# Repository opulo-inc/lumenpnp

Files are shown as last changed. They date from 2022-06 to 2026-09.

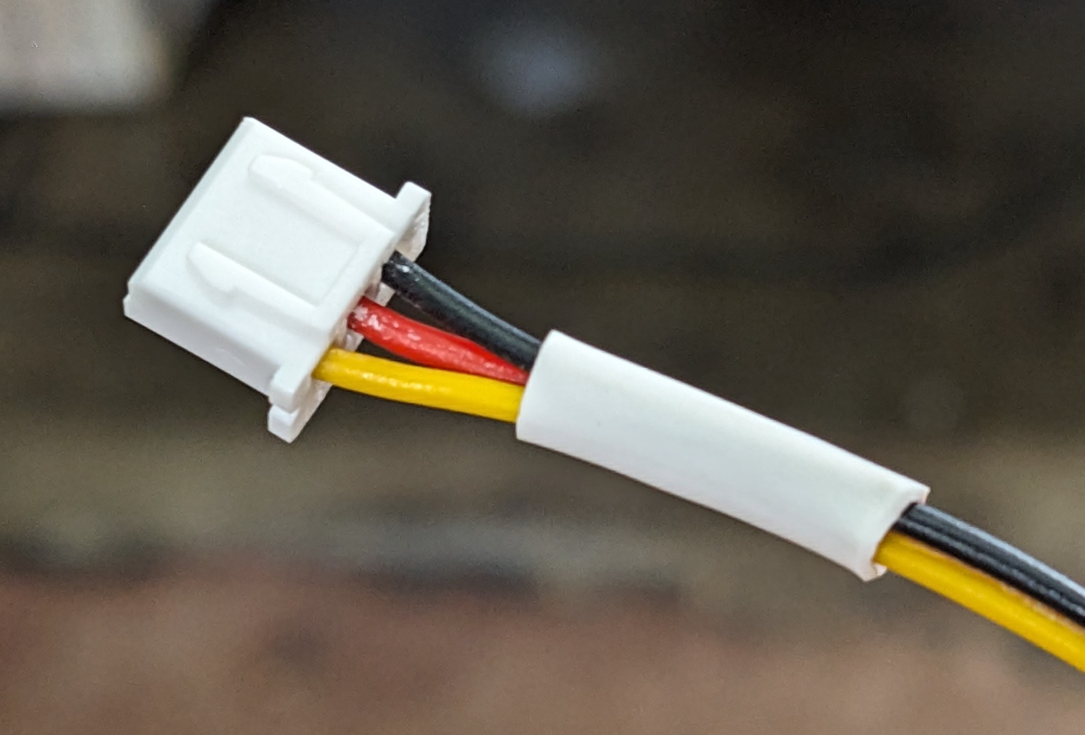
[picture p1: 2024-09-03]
src/CHA/img/label.png

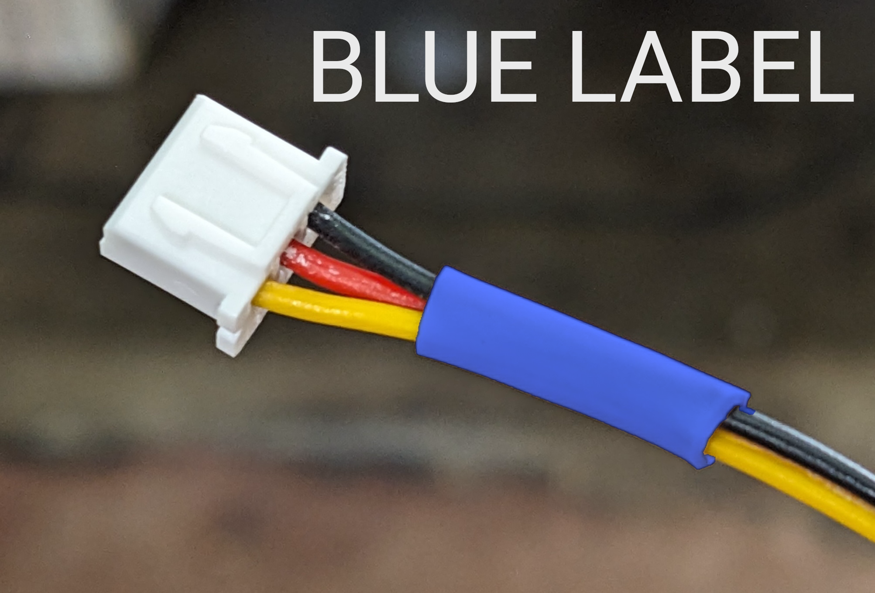
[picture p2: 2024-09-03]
src/CHA/img/label-blue.png

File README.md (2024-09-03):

# LumenPnP

The LumenPnP is an open source [pick and place machine](https://en.wikipedia.org/wiki/Pick-and-place_machine) that reliably and accurately assembles electronic components onto circuit boards.

v4

The LumenPnP is available for sale on the [Opulo Website](https://www.opulo.io/products/lumenpnp). Machines are being used in active production daily. If you build or buy one, please help the project by documenting bugs with a GitHub issue.

**Please [read the wiki here](https://github.com/opulo-inc/lumenpnp/wiki)!** The wiki covers information about the state of the project, contributing instructions, and frequently asked questions.

Along with the pick and place machine itself, the project also includes feeders designed to work with the machine. The source for powered feeders can be found [in their separate repository](https://github.com/opulo-inc/feeder).

For exported versions of the source (STLs, schematic PDFs, compiled binaries, etc), you can find them attached to the [latest release](https://github.com/opulo-inc/lumenpnp/releases).

The LumenPnP's development process is being cataloged in a series of videos. A playlist of these can be found [here](https://www.youtube.com/playlist?list=PLIeJXmcg1baLBz3x0nCDqkYpKs2IWGHk4).

## How do I get one?

You can buy a machine on the [Opulo Website](https://www.opulo.io/products/lumenpnp)!

## Contributing

If you would like to contribute to the project, awesome! Check out the [contributing page](https://github.com/opulo-inc/lumenpnp/wiki/Contributing) to get started.

## Community

Discussion about the project happens on the [LumenPnP Discord server](https://discordapp.com/invite/TCwy6De)!

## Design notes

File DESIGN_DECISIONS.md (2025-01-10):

# LumenPnP Design Decisions

This page aims to illustrate the design decisions behind the LumenPnP. The design process started in early 2020, and has seen hundreds of iterations and approaches. This page gives background about why things are done the way they are, to help communicate to folks new to the project what has been tried, and why it was not chosen.

## Overview

The LumenPnP is a mostly 3D printed desktop pick and place machine. It has two nozzles on the head. There are two built-in cameras and ring lights for top and bottom vision. These are used for fiducial calibration of the board being populated and part rotation/offset calibration on the nozzle. It is capable of populating boards as large as 225mm x 400mm.

The LumenPnP is comprised of v-slot aluminum extrusion for most of the structural members in the machine, connected together using aluminum brackets and 3D printed parts. The X gantry rides on two Y gantries, and v-slot wheels are used for linear motion in the machine. The main build area of the machine is comprised of staging plates, which are 120mm x 600mm PCBs with a [Peek Array](https://www.crowdsupply.com/sutajio-kosagi/novena) for mounting machine parts and strip feeders.

## Axis of Motion

There are five axes of motion in a stock LumenPnP:

- The X linear axis is driven by a NEMA 17 stepper motor that pulls the X gantry along an MGN12H linear rail using a GT2 timing belt.
- The Y linear axis is similar, but uses two two NEMA 17 stepper motors and two MGN12H linear rails. These motors are independently driven by two stepper drivers as of v4.0.0.
- The Z linear axis is mounted to the X gantry and also uses a NEMA 17 stepper motor, but pulls two counterweighted Z gantries along short LML9B linear rails.
- The A & B rotational axes are mounted to the Z gantries and each use a NEMA 11 stepper motor with a hollow shaft. These pass the vacuum through to the nozzles used to pick and place parts.

### V-rollers vs linear rails

V-slot rollers are small wheels designed to ride inside the V-slots on aluminum extrusions. They're an inexpensive means to support and constrain the motion of a linear axis. They became very popular due to being used on mass market 3D printers such as the Ender 3. Linear guide rails, on the other hand, are solid steel rails coupled with a carriage block containing ball bearings. Linear rails require less maintenance and perform significantly better than V-rollers, but have typically been too expensive for hobbyist machines.

Due to this, V3.0.5 and earlier versions of the LumenPnP used V-rollers for the X and Y linear axes. However, times changed and 3D printers began competing on speed which necessitated linear rails - making them much easier and cheaper to source. As a result, Opulo switched the LumenPnP to linear rails going forward.

If you want to replace the V-rollers on an existing LumenPnP with linear rails you can use [Stargirl's mod](https://www.printables.com/model/278803-lumenpnp-linear-rail-mods-v3).

### Why not CoreXY?

CoreXY offers the possibility of faster movement by removing a heavy motor from one of the gantries, keeping the head very light and easy to accelerate.

However, switching to a CoreXY configuration would actually *remove* a motor from the current system. The current solution has two separate stepper motors dedicated to moving the Y gantry, and one motor for the X gantry. CoreXY would reduce this to only two motors shared across both axis, which actually results in an lower average acceleration.

Also, CoreXY has a much more complicated belt routing path than with a separate X and Y axis configuration. Keeping axes separate allows Opulo to ship each axis packaged separately, meaning belts are pre-routed making assembly much easier.

### Why not a NEMA 8 hollow shaft for part rotation?

In the early days of design, we struggled to find a full 360 degree pneumatic coupler for 4mm PU tubing with a M5 threading at a decent price that didn't leak like a sieve. This coupler was meant to thread into the top of the hollow-shaft steppers that rotate parts on the nozzles. Because we couldn't get a good coupler, we were forced to limit the A and B axis rotation to plus or minus 180 degrees as to not tangle up the tubing, as opposed to being able to rotate any amount in any direction. Even then, the tubing provided enough resistance to rotation that a beefier stepper was required to ensure we weren't skipping steps when rotating nozzles.

Since then, the community has found sources for much better couplers that eliminate this problem. With almost no resistance to rotating nozzles, much smaller motors can be used. This is an update Opulo is actively exploring rolling into production, especially in conjunction with a linear rail/CoreXY update where the benefit of this weight reduction would be realized.

## Firmware

The LumenPnP runs stock Marlin firmware. Marlin was originally designed to control 3D printers, but it works spectacularly for controlling a pick and place machine. We've added a couple features to Marlin to support pick and place specific functions, namely reading vacuum sensors and communicating to feeders.

### Why not a different firmware project?

There exist many different 3D printer/CNC firmware projects, of which a number would likely work well for a pick and place. We ended up choosing Marlin for a number of reasons.

The first and primary reason for choosing Marlin is the ease of adding new hardware to mainline. Marlin supports hundreds of different controller boards, and adding a new one is a well understood process. This also means any pick and place specific features we add upstream are able to be used by folks on hundreds of other hardware designs.

Other options like Klipper would definitely fulfill the requirements of the project, but many of the features of these other options are unnecessary for a pick and place application.

## Motherboard

The LumenPnP motherboard is a custom controller based on the STM32F407VET6 microcontroller. It has support for up to 6 axis of motion, four pumps or valves, two vacuum sensors, two WS2812 busses, an RS-485 port for feeder communication, and an AUX port for peripherals.

### Why not off the shelf?

Some off the shelf boards would work great for the core functionality of a pick and place. We wanted to provide new features specific to pick and place machines that are not available in other hardware. The main features we wanted to add were vacuum sensors for detecting if parts have been successfully picked, and a port to provide power and communication for feeders.

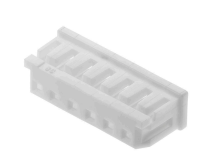
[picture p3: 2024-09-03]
src/CHA/img/molex-51065-0600.png

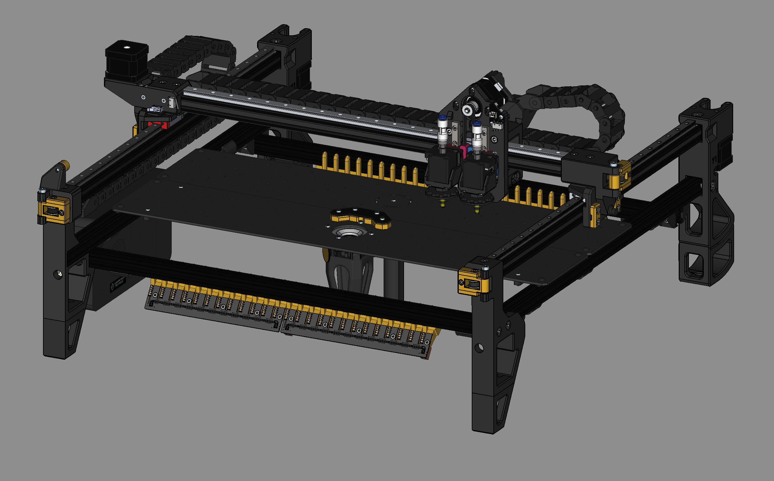
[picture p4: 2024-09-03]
img/v4-cad-hero.png

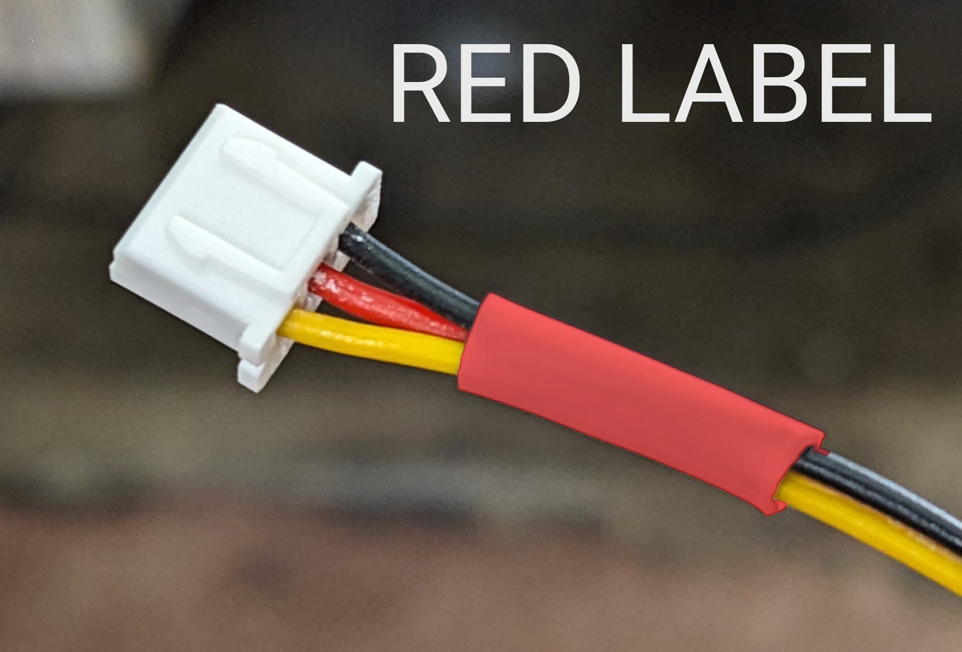
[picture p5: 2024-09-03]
src/CHA/img/label-red.png

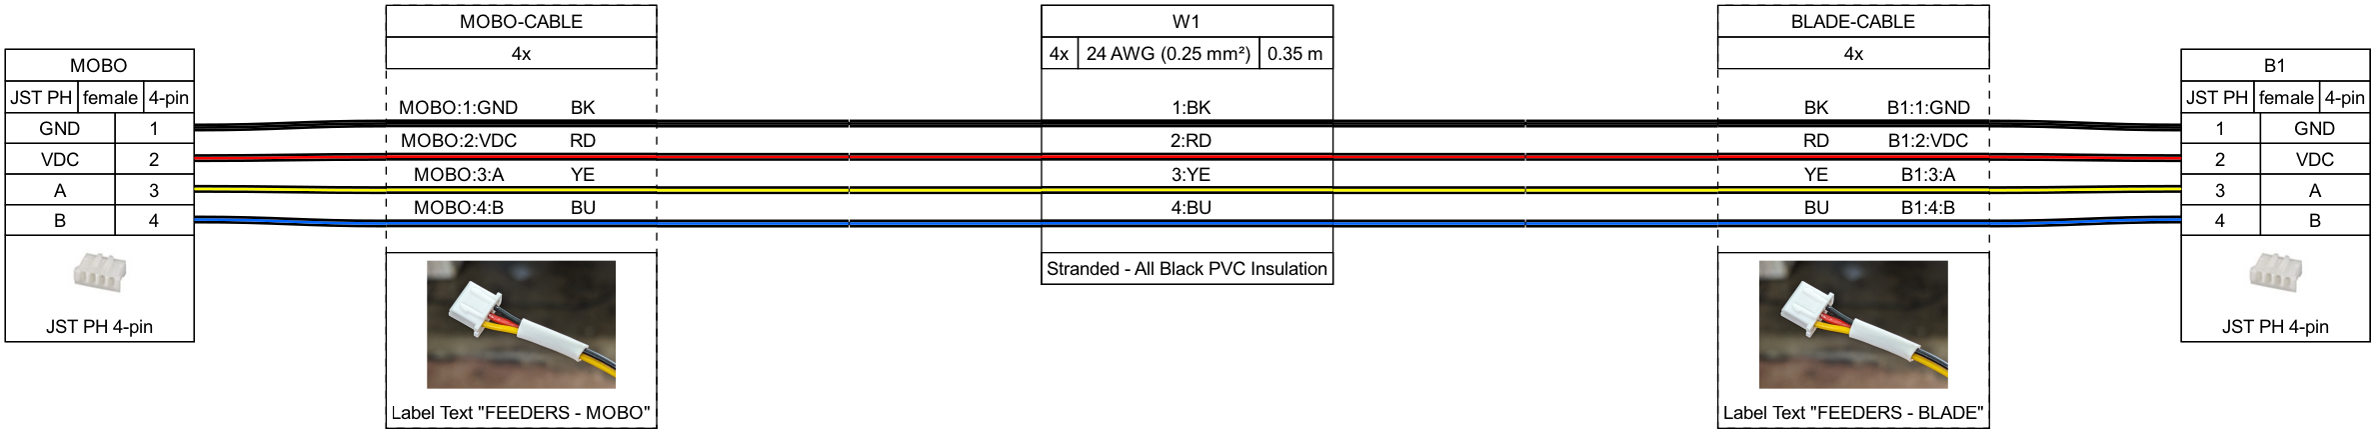
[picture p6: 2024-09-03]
src/CHA/mobo-blade1/mobo-blade1.png

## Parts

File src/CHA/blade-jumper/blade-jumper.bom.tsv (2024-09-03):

Id | Description | Qty | Unit | Designators
1 | Cable, 4 x 24 AWG | 0.04 | m | W1
2 | Connector, JST PH, female, 4 pins | 2 |  | J1, J2

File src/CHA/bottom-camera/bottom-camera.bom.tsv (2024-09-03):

Id | Description | Qty | Unit | Designators
1 | Cable, 4 x 24 AWG | 0.7 | m | W1
2 | Connector, JST ZH, female, 4 pins | 1 |  | BC-C
3 | Connector, USB TYPE A, male, 4 pins | 1 |  | BC-H
4 | Wire, BK | 0 | m | BL-H-CABLE, BL-M-CABLE
5 | Wire, RD | 0 | m | BL-H-CABLE, BL-M-CABLE
6 | Wire, YE | 0 | m | BL-H-CABLE, BL-M-CABLE

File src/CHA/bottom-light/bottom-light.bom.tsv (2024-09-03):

Id | Description | Qty | Unit | Designators
1 | Cable, 3 x 24 AWG | 0.35 | m | W1
2 | Connector, JST PH, female, 3 pins | 1 |  | BL-M
3 | Connector, JST XH, female, 3 pins | 1 |  | BL-H
4 | Wire, 22 AWG, RD | 3.1 | m | BL-H-CABLE, BL-M-CABLE
5 | Wire, 22 AWG, WH | 3.1 | m | BL-H-CABLE, BL-M-CABLE
6 | Wire, 22 AWG, YE | 3.1 | m | BL-H-CABLE, BL-M-CABLE

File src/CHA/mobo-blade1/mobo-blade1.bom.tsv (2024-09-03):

Id | Description | Qty | Unit | Designators
1 | Cable, 4 x 22 AWG | 0.8 | m | W1
2 | Connector, JST PH, female, 4 pins | 2 |  | B1, MOBO

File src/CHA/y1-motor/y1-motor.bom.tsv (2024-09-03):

Id | Description | Qty | Unit | Designators
1 | Cable, 4 x 22 AWG | 0.8 | m | W1
2 | Connector, JST PH, female, 6 pins | 1 |  | X2
3 | Connector, JST XH, female, 4 pins | 1 |  | X1

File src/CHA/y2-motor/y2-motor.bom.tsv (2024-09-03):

Id | Description | Qty | Unit | Designators
1 | Cable, 4 x 22 AWG | 1.2 | m | W1
2 | Connector, JST PH, female, 6 pins | 1 |  | X2
3 | Connector, JST XH, female, 4 pins | 1 |  | X1

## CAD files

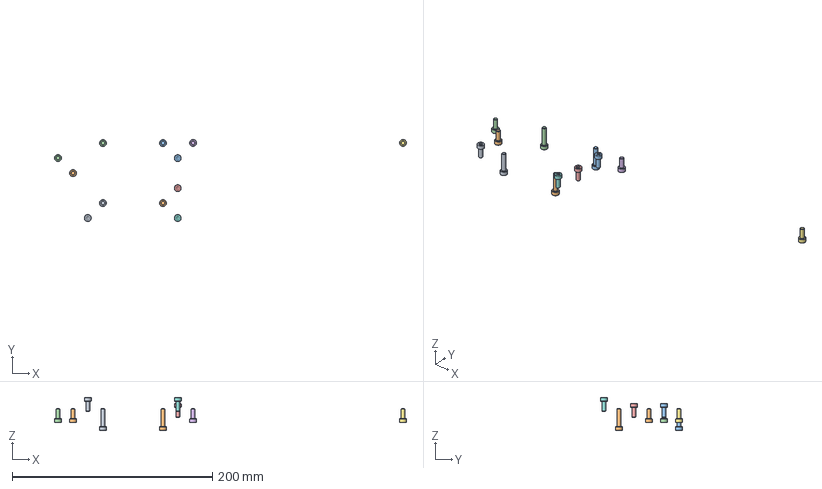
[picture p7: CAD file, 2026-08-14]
src/ASM/staging-plate-ASM.FCStd
352.0 x 82.1 x 33.3 mm
M4x18-Screw
M4x10-Screw
M4x10-Screw002
M4x10-Screw004
M4x10-Screw006
M4x10-Screw008
M4x10-Screw010
M4x10-Screw012
M4x10-Screw014
M4x18-Screw002
M4x18-Screw004
M4x18-Screw006

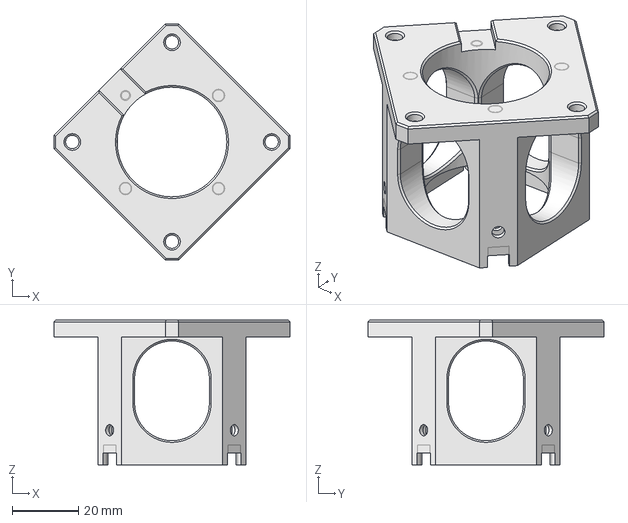
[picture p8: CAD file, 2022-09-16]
pnp/cad/FDM/bottom-camera-mount.FCStd
71.0 x 71.0 x 43.5 mm

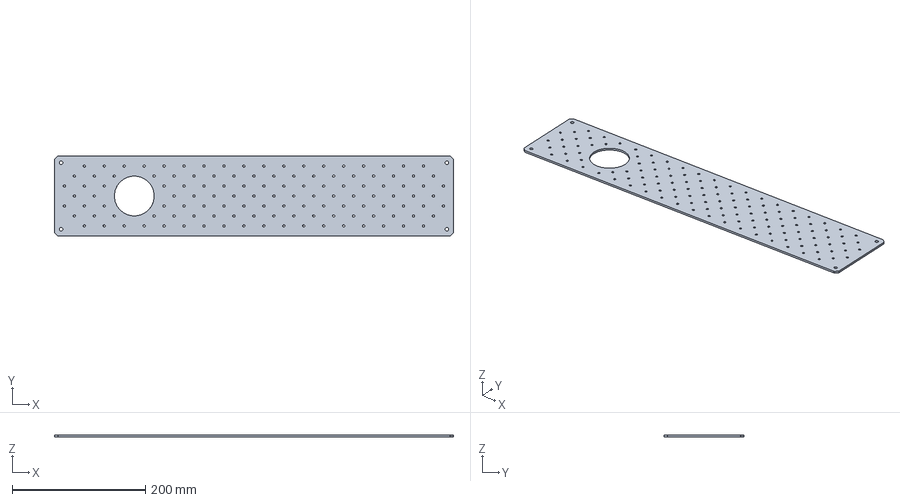
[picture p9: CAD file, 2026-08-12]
src/CSM/staging-plate-offcenter.FCStd
600.0 x 120.0 x 3.00 mm

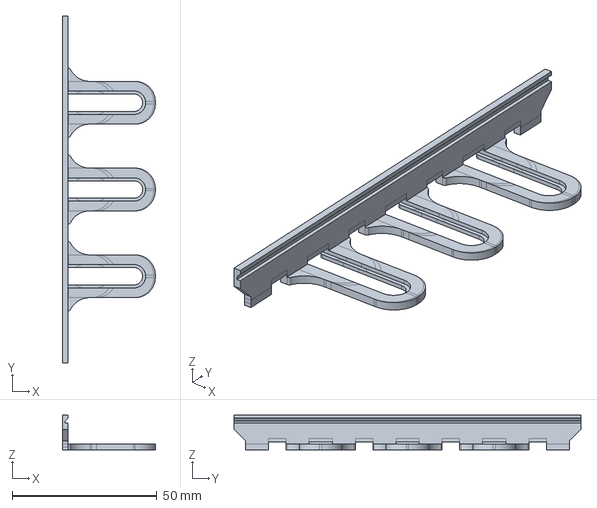
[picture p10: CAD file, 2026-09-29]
src/FDM/adj-strip-feeder-left.FCStd
32.1 x 120.0 x 12.0 mm

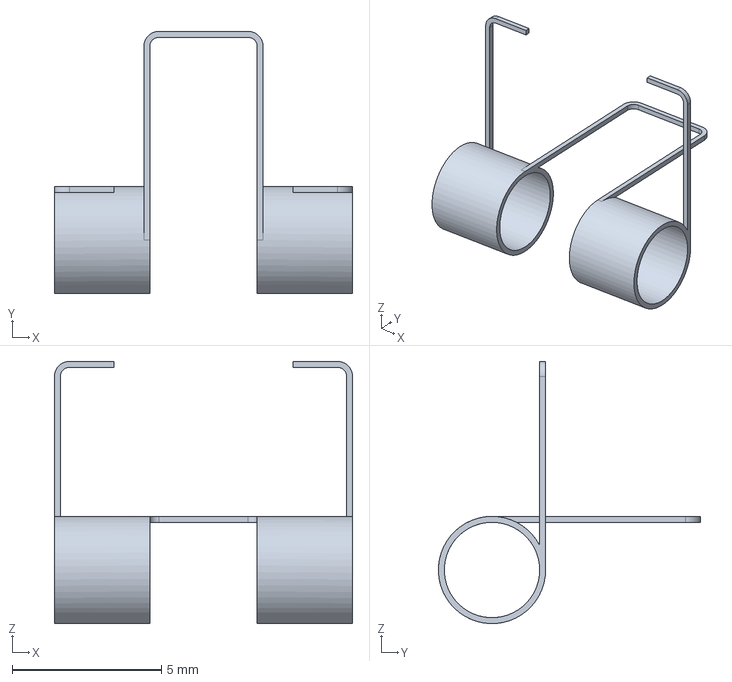
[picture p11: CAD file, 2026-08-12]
src/OTS/dt-spring-pick-window.FCStd
10.0 x 8.80 x 8.80 mm

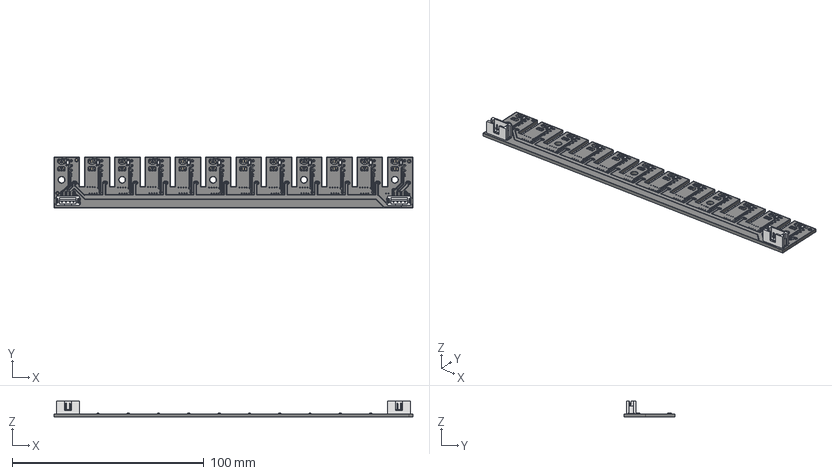
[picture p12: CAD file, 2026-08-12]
src/PCB/blade12/blade12-PCB.FCStd
187.2 x 26.6 x 8.22 mm
Pcb_f782
topPads_f782
topTracks_f782
topZones_f782
botPads_f782
botTracks_f782
botZones_f782
${REFERENCE}_R_0805_2012Metric_null x 12
${REFERENCE}_B4B-PH-SM4-TB_null[2] x 2

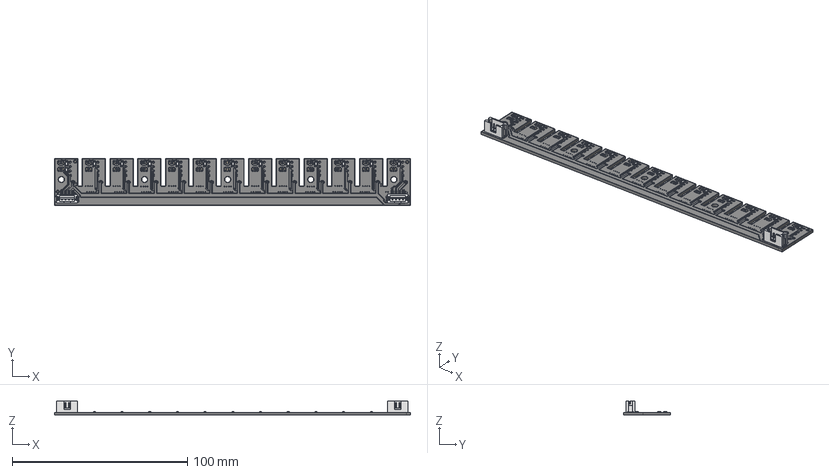
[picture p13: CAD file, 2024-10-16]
src/PCB/blade13/blade13-PCB.FCStd
203.0 x 26.6 x 8.22 mm
Pcb_e7a3
topPads_e7a3
topTracks_e7a3
topZones_e7a3
botPads_e7a3
botTracks_e7a3
botZones_e7a3
${REFERENCE}_R_0805_2012Metric_null x 14
${REFERENCE}_B4B-PH-SM4-TB_null[2] x 2

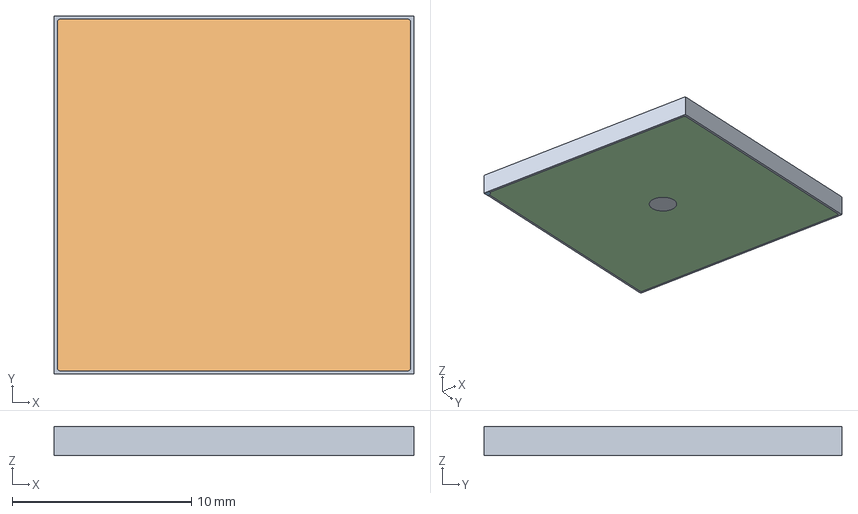
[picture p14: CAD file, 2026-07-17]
src/PCB/cal-fid/cal-fid.FCStd
20.0 x 20.0 x 1.63 mm
Pcb_c21e
topZones_c21e
botPads_c21e_cut
botZones_c21e

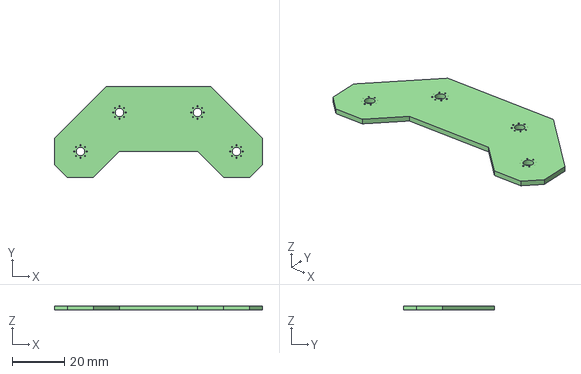
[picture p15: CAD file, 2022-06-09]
src/PCB/datum/datum-board.step
80.0 x 35.0 x 1.60 mm

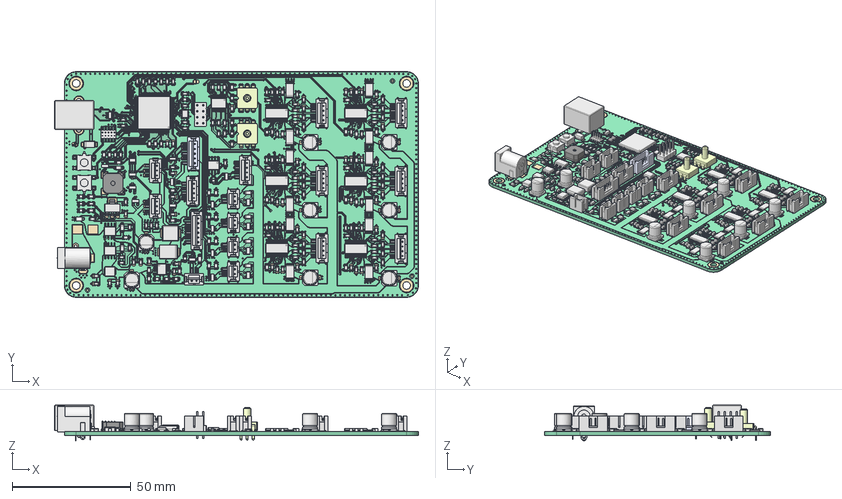
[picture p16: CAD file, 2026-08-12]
src/PCB/mobo/mobo-REV05.FCStd
153.1 x 95.0 x 15.0 mm
Pcb_270f
topPads_270f
topTracks_270f
topZones_270f
botPads_270f
botTracks_270f
botZones_270f
C19_C_0805_2012Metric_dd7fe1078c82 x 116
U2_SO-8_3.9x4.9mm_P1.27mm_18ac448d4230 x 2
C18_CP_Elec_63x77_ff28b986d17e x 8
J18_B2B-PH-SM4-TB_b9beb4a1e8ac[2] x 5
J5_B4B-PH-SM4-TB_7cb4547b0ad5[2] x 8
R61_R_0805_2012Metric_702471a57eb5 x 58
L2_L_Sunlord_MWSA0402S_521b67255e56
Q6_SOT_23_7e3c471798a1 x 13
D7_D_SOD_123F_3f376ee7206a x 6
R32_R_2512_6332Metric_fd8a2fdd02c5 x 12
U21_TSOT_23_401a1807623d x 4
J17_B5B-PH-SM4-TB_ce0894eb786b[2]
BZ1_CUI_DEVICES_CMT-8504-100-SMT-TR_9afe1c6a999b[2]
L12_L_0805_2012Metric_ae928abe879c x 24
J13_B6B-PH-SM4-TB_f104a4ad5df6[2]
U15_SOIC_8_39x49mm_P127mm_9e3604cb9ea4 x 2
D3_D_SOD_123_7fd80e287a01 x 2
D19_D_SMA_ff0e973445e4
U17_TSSOP_20_44x65mm_P065mm_3a2178bb8b3e
D1_D_SMC_db09bdd7a7d4
U12_SOT_23_6_22d69487b26d x 2
SW1_B3S_110[]_fa0ae1ab19d8[2] x 2
J7_BarrelJack_Horizontal_6e7f0b02579b
U10_HTSSOP_28_1EP_44x97mm_P065mm_9ebe34d6a526 x 6
D20_D_SMF_c34d6fe6dce6
U5_LQFP_100_14x14mm_P05mm_e908b35d191a
D5_LED_0805_2012Metric_18e83e1d4d5c x 3
J2_PinHeader_2x05_P127mm_Vertical_SMD_7237c33a1887
J9_B3B-PH-SM4-TB_472ac10851bf[2] x 2
L1_L_Sunlord_MWSA0603S_998824e03534
J14_PinHeader_2x04_P254mm_Vertical_97425652c6a4
Y1_Crystal_SMD_3225-4Pin_3.2x2.5mm_5af4ee45a679
U4_SOT_223_0cafcd1d99c6
XGZP6857D200KPGPN33_002
XGZP6857D200KPGPN33_001
USB type-B female PCB

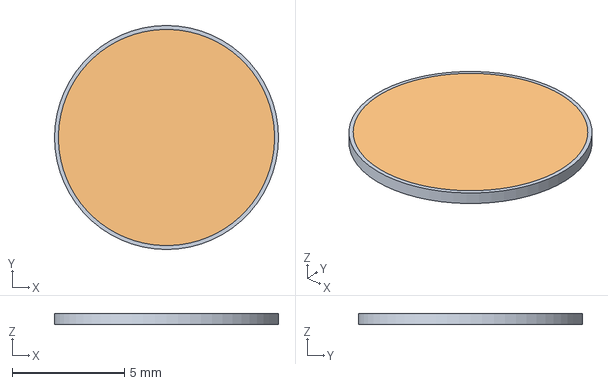
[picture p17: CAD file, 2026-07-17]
src/PCB/nozzle-cal-token/nozzle-cal-token.FCStd
10.0 x 10.0 x 0.51 mm
Pcb_83d9
topZones_83d9

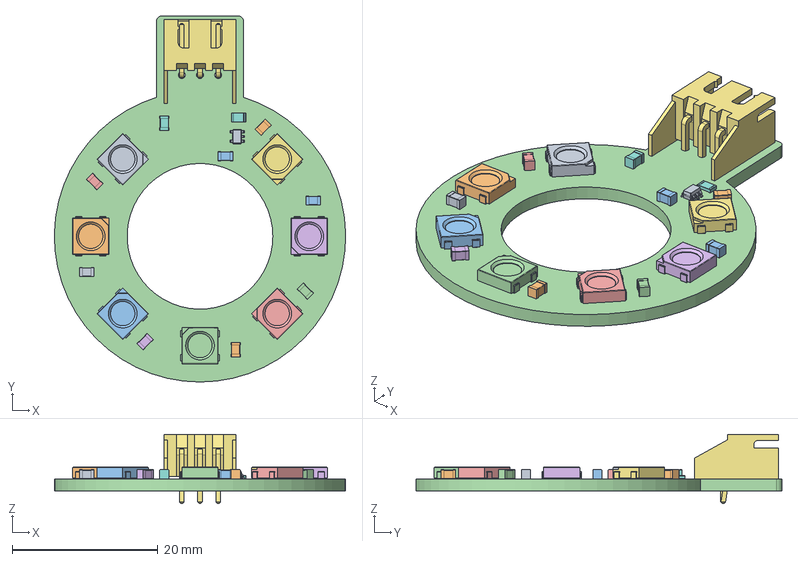
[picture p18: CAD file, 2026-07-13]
src/PCB/ringLight/bottom-ring-light.FCStd
40.0 x 50.2 x 9.50 mm
bottom-ring-ligh-pcb001

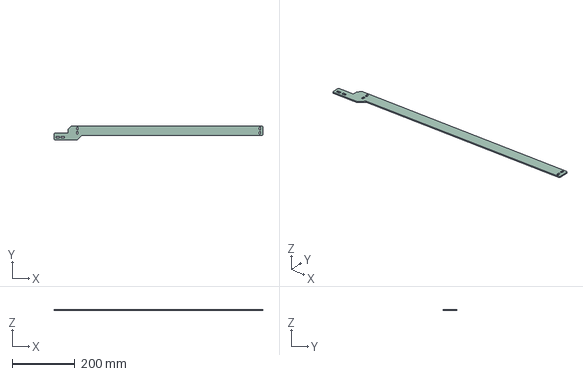
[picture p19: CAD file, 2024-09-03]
src/PCB/x-cable-chain-support/x-cable-chain-support.step
664.0 x 44.5 x 3.00 mm

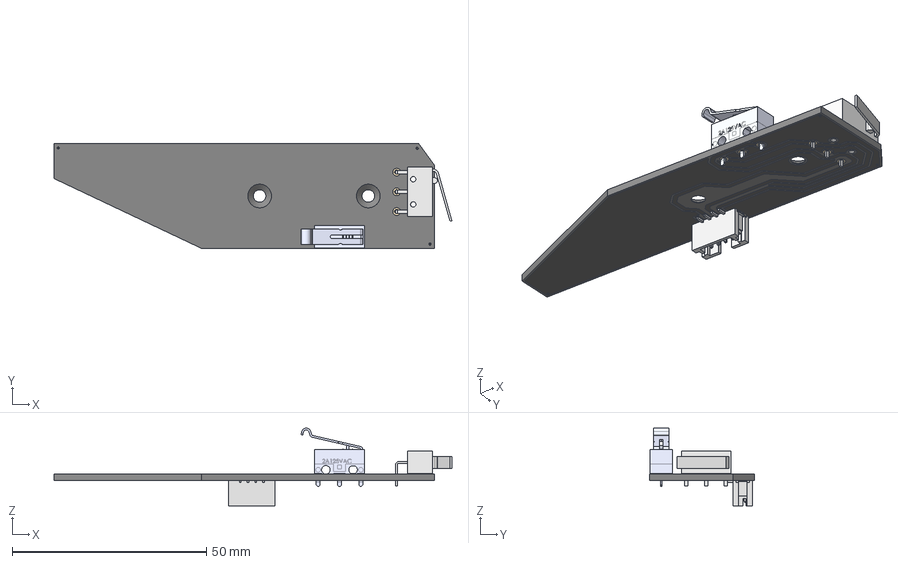
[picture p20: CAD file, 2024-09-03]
src/PCB/xy-limit/xy-limit.FCStd
102.6 x 27.0 x 20.1 mm
topPads_14f9
botPads_14f9
botTracks_14f9
botZones_14f9
Pcb_14f010
SW2_Limit_Switch_SPDT_sim_roller_8e450556c7f0
SW1_Body_0292104bbb26
J2_B4B-PH-SM4-TB_56e32e6460db[2]

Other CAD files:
src/ASM/board-mount-dynamic-ASM.FCStd
src/PCB/z-limit/z-limit.FCStd
pnp/cad/FDM/x-gantry-back.FCStd
src/CSM/build-plate.FCStd
src/FDM/12mm-strip-feeder.FCStd
src/FDM/16mm-strip-feeder.FCStd
src/FDM/24mm-strip-feeder.FCStd
src/FDM/32mm-strip-feeder.FCStd
src/FDM/8mm-strip-feeder.FCStd
src/FDM/adj-strip-feeder-right.FCStd
src/FDM/back-leg-extension.FCStd
src/FDM/back-leg.FCStd
src/FDM/belt-clamp.FCStd
src/FDM/belt-tension-arm.FCStd
src/FDM/blade12.FCStd
src/FDM/blade13.FCStd
src/FDM/board-mount-dynamic.FCStd
src/FDM/board-mount-flap.FCStd
src/FDM/board-mount-static.FCStd
src/FDM/board-support.FCStd
src/FDM/bottom-camera-mount.FCStd
src/FDM/bottom-light-mount.FCStd
src/FDM/bottom-vision-cable-clamp.FCStd
src/FDM/bottom-vision-cover.FCStd
src/FDM/cable-splay.FCStd
src/FDM/cal-fid-mount.FCStd
src/FDM/control-box-lid.FCStd
src/FDM/control-box.FCStd
src/FDM/datum-board-mount.FCStd
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

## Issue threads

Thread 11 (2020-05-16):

Change carriage bottom rollers mounting for eccentric nut

Frzoen, 2020-05-16:
Change design of the carriages to use eccentric nut.
ie. this [Eccentric Spacers - Amazon](https://www.amazon.com/PSCCO-Eccentric-Spacers-Wheel-Printer/dp/B083YTJ7S3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)

This will help in tightening the carriage rollers onto aluminium profiles.
This is also opportunity to change the design to use one less roller/carriage by changing square pattern to triangle. This shouldn't impact stability of carriage and help tightening BOM.

sphawes, 2020-05-16:
I love these things, but I'm concerned about their usage here. Instead of being inserted into a hole on a nice piece of steel, they'd be going into a hole on an FDM part. I'm not currently super happy with the current slot method, so definitely looking for an alternative, but these in a printed part might end up causing problems. Are there other types of tensioning we could use for these rollers? Or maybe some way we could have these eccentric spacers slot into something a bit more substantial?

Frzoen, 2020-05-16:
Just finished design for eccentric nut.

I will print it and test with one salvaged from my printer. Will get in touch soon with test resoults

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

Frzoen, 2020-05-16:
Maybe mounting mechanism similar to this from EleksMaker featured in Marco Reps's videos?
[mentioned video](https://youtu.be/1hFNj86L7sk?t=120) (mind the goat).

There is sheet of acrylic... maybe 3d print will be similar in strength.

Frzoen, 2020-05-17:
Ok, so after first test that looks promising.

For now i cannot test it with stepper motor but i tried to break it using a lot of force and taking advantage of the lever with 2020 profile and I could't break it.

Right now i will adjust the height of the spacers for the v-slot rollers.

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

G-Pereira, 2021-02-14:
As discussed this change would require increased maintenance since the nuts would loosen over time and also not the best to use against FDM parts.

Closed 2021-02-14.

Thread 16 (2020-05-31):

Suggestion to change nema11 hollow shaft to a different system for angular positioning

Arthur-Silveira, 2020-05-31:
I was thinking about changing the Nema11 with hollow shaft to a different angular positioning system.
It seems to be very difficult to find such a motor here in Brazil, so I'm planning on using the same standard NEMA17 used on other axes.
I will try the approach on this drawings (really sorry for the ultra low quality on hand drawing, absolutely nothing is on scale).

Any thoughts to improve this idea??

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

Arthur-Silveira, 2020-05-31:
Nevermind for this suggestion.
I'll have to import the nozzle and nozzle adapter anyways, so I will just add the motor to the list as well.

I'm thinking about this kit from Aliexpress instead of the RobotDigg suggested on the BOM

https://www.aliexpress.com/item/4000090366591.html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,scm-url:1007.13338.170725.0,pvid:1c21acfd-dd72-44ef-a7ba-3e56ca9c6147,tpp_buckets:668%230%23131923%2316_668%23808%234093%23765_668%23888%233325%2315_3338%230%23170725%230_668%232846%238111%23469_668%232717%237565%23778

bjonesrock, 2020-06-01:
I'm working on putting together a pnp as well, and didn't want to buy the RobotDigg kit either. I bought NEMA8 steppers with hollow shafts, and juki nozzles from ebay and then bought quick connect fittings with 1/4" NPT threads.

I printed a cap that screws into one side of the NEMA8 motor with M2x20 screws and then the quick connector fitting screws into the cap. Super cheap and simple way to replace the swivel adapter with a common part and a 3d printed part.

I also printed an adapter to connect the 5mm hollow NEMA8 shaft to the 7mm Juki shaft, but it's not perfectly centered, which I don't like.

Here are some photos and the STEP files for the NEMA8 cap and the Juki adapter.
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
[juki-nema8-connectors.zip](https://github.com/sphawes/index/files/4711643/juki-nema8-connectors.zip)

Arthur-Silveira, 2020-06-02:
Hi bjonesrock,

> I printed a cap that screws into one side of the NEMA8 motor with M2x20 screws and then the quick connector fitting screws into the cap. Super cheap and simple way to replace the swivel adapter with a common part and a 3d printed part.

Printing that cap seems to be a very good low cost option to replace the swivel connector. It might add some vacuum losses due to air leaking through the motor, but not sure if enough to affect operation.
I will definetely give a try to your idea before purchasing the Aliexpress one. I think I might find a similar motor here. This way i will only have to buy the nozzle from ebay or Ali.

> I also printed an adapter to connect the 5mm hollow NEMA8 shaft to the 7mm Juki shaft, but it's not perfectly centered, which I don't like.

Yeah, I'm very concerned about the angular repeatability due to the misalignment. I've seen someone complaining about this on that aliexpress solution I've posted the link previously as well (posting that it would make not viable to place even 0603 components, even using the original Juki adapter).

I was wondering if we could add extra support with a ball bearing on one of those positions (see picture below). The problem on the extra support on the red arrow is that it will make very difficult to change the nozzle, so probably on the blue arrow is better.

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

bjonesrock, 2020-06-02:
Additional support would probably help, but it's not that long. The hollow end of the stepper shaft is basically right up against the back of the juki nozzle. I wonder if I used a resin printer if the tolerances would be better. I feel like the coupler just isn't straight enough.

Arthur-Silveira, 2020-06-03:
I see your coupler is quite simple. I though it originally had more inner details to fit the nozzle.

Have you considered just printing a simple cylinder with a single and slightly smaller hole (say 4mm) in the middle, then drill the entire piece for 5mm , and then backdrill only partially for the bigger  (7mm) hole for the nozzle?
I believe it might reduce the centering misalignment (of course, depending of the bit drill and driller quality).
Or if you have access to a turning machine, even better just machine the entire part from a solid piece of nylon, of course.

Maybe another possible try is to use a commercial 5x7 shaft coupling and then cover it with some tape to keep vaccum inside.
(like https://pt.aliexpress.com/item/32826916374.html)

bjonesrock, 2020-06-03:
All good ideas. No I haven't tried just drilling it out, I'll give that a go tomorrow and see how it works. I wish I had a lathe, though I haven't had many good reasons to get one.

Hmm those flexible adapters have slots cut out which would need to be covered with some electrical tape. I just bought a pair from Amazon and will test it out

Thanks!

bjonesrock, 2020-06-03:
I tried printing it with slightly smaller holes and then drilling it with M5 and M7 drill bits on my drill press and it's not any better.

I also then tried drilling a small piece of wood with the M5 bit, and then in the same hole drilling halfway through with an M7 bit and that wasn't any better either.

The 5mm to 7mm coupler comes in the mail tomorrow and I'll let you know how that goes.

I haven't used Open PNP before, but using the bottom camera could it compensate for an off center rotation with the upward facing camera?

plasticuser, 2020-06-04:
I wonder why NEMA 11 was chosen to replace NEMA 8? Is the NEMA 8 underpowered? It has the same accuracy, is lighter and draws less power than the 11. It’s a bit quicker too.

Mostly, it’s available from many more outlets in the hollow shaft variant.

It would be helpful to know the reason behind the decision, so we can buy the right parts and move on.

bjonesrock, 2020-06-05:
Yeah NEMA 8 motors make way more sense to me and seems to be what most people use. The flexible adapters aren't coming until Saturday so I tried adding 3 screws around the 3d printed coupler to see if I could straighten it out. But it's still not great.
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

plasticuser, 2020-06-05:
The NEMA 8 are a fair bit lighter than the NEMA 11 versions, so I suspect the carriage lift/return would manage much better acceleration.

bjonesrock, 2020-06-08:
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

I finally got the 5mm to 7mm coupler in the mail.

It works great! It spins nice and centered. You just have to put some pressure down on the coupler as you tighten it so everything stays nice and square

Here is a link to the coupler I bought off Amazon https://www.amazon.com/dp/B0816JQBYZ/ref=cm_sw_r_other_apa_i_3zS3EbKDBYFMK

bjonesrock, 2020-06-08:
Uhh actually scratch that. The flexible coupler is solid in the center. I tried drilling a hole in the rubber plastic center and putting electrical tape around the coupler but when I blow through the hollow motor shaft the air escapes through the sides of the coupler

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

Arthur-Silveira, 2020-06-17:
> Uhh actually scratch that. The flexible coupler is solid in the center. I tried drilling a hole in the rubber plastic center and putting electrical tape around the coupler but when I blow through the hollow motor shaft the air escapes through the sides of the coupler
>

Maybe using this kind of commercial coupler would be beter to avoid leakage. Some tape over the grooves (even over screws) seems to be enough.
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

Unfortunately, I've not yet managed to find a suitable hollow shaft motor here in BR.
For now, I will wait for the complete kit I've purchased on Ali (https://pt.aliexpress.com/item/4000090366591.html) as amazon is not an option for me.
If anyone else find suitable options on Chinese vendors, that would be welcome.

Also, hoping the bottom camera could adequately compensate for some deviations due to misalignment.

bjonesrock, 2020-06-17:
Yeah that style adapter seems like it might work better. I tried another 3D printed adapter that has 2 flanges that an M2 screw goes into to pull the coupler tight, but it was slightly off center as well.
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
bjonesrock, 2020-06-29:
Yeah that might do the trick. In the US we call that Plumber's Putty. I've got some plasticine clay on hand, maybe that'll work. I had to rotate the part in order to print it without supports so it has lots of layer lines which makes sense why it wouldn't seal very well.

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

Arthur-Silveira, 2020-06-30:
If it is also leaking between the layers even with finer layer steps (0.1 mm layer for example) maybe some paint or coating might help reducing the leakage. Maybe some spray painting, or nail polish ? Never tried painting PLA before.. there might be some preferred options that best adhere to PLA plastic.

This seems very good, but very specific though
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
 https://3druck.com/3d-druckmaterialien/xtc-3d-verleiht-3d-gedruckten-objekten-eine-ebenmaessigere-oberflaeche-3028167/

I would give a try with nail polish + commercial Oring (to avoid the mess with the Plumber's putty) as 1st option, since they seem commercially available everywhere.

bjonesrock, 2020-06-30:
I put a thin layer of clay between the 3D print and the NEMA8 motor and that sealed it really well :)

Plumber's putty is pretty common, but clay works just as well. Smoothing the part might work, but PLA is harder to smooth.

Since I rotated the part to 3D print it the tolerance on the push to connect adapter was a little loose so I wrapped some more teflon tape. I'll tighten up the part and try printing it again and upload the file soon

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

bjonesrock, 2020-07-01:
Alright I tightened the hole that the push to connect fittings screw into so you don't have to seal it with extra teflon tape. Here are the updated STEP and STL files
[VacuumCapNEMA8TopGT2BeltTight.zip](https://github.com/sphawes/index/files/4859855/VacuumCapNEMA8TopGT2BeltTight.zip)
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

Arthur-Silveira, 2020-07-24:
My motor+nozzle+adapter kit finally arrived from China.
Mi kit also came with nozzle connected to what seems to be the wrong side, but first, I'm having some electrical issues.

@bjonesrock can you share the electrical connections of your motor?  (it seems to be similar to mine). Are you using 12V as well?

My little motor is pulling `ALONE` over 0,8 A (@6 V only, I've reduced the voltage because my PSU was triggering overcurent). It has to be something about wiring. When I replace this one with two NEMA17, current keeps around 0,6 A

I've measured continuity between `RED to BLACK` and also `YELLOW to GREEN`, so I`ve switched the terminals at RAMPS side (the connector at the motor is unchanged as arrived).
I've measured about 7 ohms each windings (that is about twice my standard NEMA 17 motors that have about 3.something ohms), so it is probably not the motor

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

wjsteele, 2020-07-24:
Did you adjust the trimpots to set the proper vRef?  See here if you haven't: [Pololu A4988](https://www.pololu.com/product/1182)

Arthur-Silveira, 2020-07-24:
> Did you adjust the trimpots to set the proper vRef? See here if you haven't: [Pololu A4988](https://www.pololu.com/product/1182)

I had not, thank you very much for the link.  But still wondering why I was getting lower current ratings on a motor with lower resistance on same pot. adjustment.

I don't have the motor specs, but I've put coil current to about 350 mA (about 200 mA at PSU). If I adjust to less than that, the motor does not spin right. With that current, it is spinning very smootlhy
It is getting a little warm though, but seems OK (no smell yet).

Now, I'll try to detach that coupler to place it on the other side of the shaft.
It is very misaligned: https://drive.google.com/file/d/1tLsLkWzka8an-K4w2UKLxB3A6DuTmg_x/view?usp=sharing

daveismith, 2021-02-04:
This seems stale and like the project has moved on. Should this be closed?

G-Pereira, 2021-02-04:
Indeed. NEMA 11 were picked and work best for microstepping and also have more thermal mass.
I also think we can close this @daveismith

Closed 2021-05-14.

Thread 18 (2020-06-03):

20x20 rail too small to rigidly support carriage

plasticuser, 2020-06-03:
During work the carriage can apply enough force to the rail to twist on it through the metal having very slight flex, but more from the lash in the bearings and touching surfaces.

This won't be as much of a problem near the end of the rails, where just the carriage lash exhibits, but towards the middle of the rail the effect will be enough to cause the head to shift position measurably. These uneven-by-position effects are the hardest to calibrate out in software.

The effect would worsen over time with wear, and also become more apparent if people build wider machines.

I suspect going to 20w x 40h rail for that one rail would reduce this effect by 75% or more and reduce wear on the rollers considerably. Remember, that rail is sitting on 2x 20x20 rails, one each end, so each of those rails is only carrying half the load, and the load is centered on those rails.

Arthur-Silveira, 2020-06-03:
I've not started assembling it yet, but i agree and I'm also concerned about this .
I've already purchased one exta 20x40 profiles as well for the center axis thinking about this.
Aside from the higher load, the center rail rollers (X axis) will also suffer from torsion effect due to more weight on one side. That does not seem to be the case on the Y axis. And as you already mentioned, they will share the load and carry half the weight each side. Using a wider profile seems to reduce the torque and stress on the rollers as well.

Also, some extra supports connecting with the bottom rails might help to distribute the load even more (like in this [updated picture](https://github.com/sphawes/index/pull/5) by [bennymeg](https://github.com/bennymeg)) on the Y axis.

It seems to be a good idea for me to go with the 20x40 profile on that single X axis (but its a simple guess for now, more impressions only after assembly)

plasticuser, 2020-06-03:
Doubling the beam height halves the leverage during picking, placing, tool changes....the whole time. This can only decrease slop and reduce wear. It also reduces the carriage's tendency to want to rotate in other planes too when moving, which will allow a little higher driven speed without vibration possibly bumping parts off.

sphawes, 2020-08-02:
My testing thus far has not shown that the 20x20 rail is too small to support the x gantry. If you try building with a 20x20 size rail and notice issues related to this rail size, please reopen this issue and we'll take a crack and changing the size. In the meantime I'll close this issue.

Closed 2020-08-02.

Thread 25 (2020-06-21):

CH340G

CrashOverrideProductions, 2020-06-21:
have you thought of using a FTDI chip for the usb to serial for the ATMega..

in my experience the CH340G has caused issues in some of my designs (automotive diagnostic tools) usually just poor performance and compatibility issues with MacOS, these could just be my implementation but ive found the FT230x chip is more reliable, plus at least in the land down under is cheaper than the CH340G $7 vs $3

plasticuser, 2020-06-21:
As a former FTDI user with a memory, I recall when FTDI bricked products with non-compliant (counterfeit) chips. FTDI bricked a lot of gear this way. There's a reason FTDI USB chips are cheaper than they used to be - FTDI destroyed their reputation by trying too hard to maintain it.

I use devices on my MacBook Pro daily that have the CH340G, and have incorporated it into various ATmega designs without issue. However, I go to some lengths to make sure I am buying genuine WCH parts, not counterfeits.

bjonesrock, 2020-06-21:
Yeah I second plasticiser. No one trusts FTDI anymore. There are tons of chips in the gray market and it's hard to know if you have real or fake chips. I'd highly advise against using FTDI.

CrashOverrideProductions, 2020-06-21:
FTDI Gate was a big pain for me, i had i heap of cheap gear stop working during development (obviously counterfit) but never had an issue with any of it since i started buying from mouser or digikey,  was just a thought with the issues ive had with CH340 but thats more than likley specific to what i was trying to do with it (single wire data bus with a non standard baud rate)

brainstorm, 2020-06-21:
I would actually discourage using the CH340 since it'll be EOL'd in OSX soon and there are more modern alternatives:

https://www.electronics-lab.com/ch551-1-80-usb-mini-development-board-based-8-bit-c51-micro-controller/

Perhaps even throw in USB-C while you are at it? You could even get rid of the barrel jack connector and power most of the board via USB-PD?... rabbit hole, I know, but also a bit more future-proof?

soundstorm, 2020-06-21:
I'm using 340C on my products, as I then can save the resonator or in this case crystal and capacitors.

sphawes, 2020-06-25:
the EOL on CH340 is the most worrisome part of this for me. ultimately, we'll be switching to a nice beefy ARM chip for the processor with native USB, so we can completely remove a USB <> UART bridge entirely. thanks all for the thoughts!

brainstorm, 2020-06-25:
... @sphawes or an ESP32S2 which has native USB and wifi "for free" ;)

adlerweb, 2020-06-26:
> ... ESP32S2 which has native USB and wifi "for free" ;)
...and probably the same famously bad performance for time sensitive applications as it's predecessors. Interrupt delays are a pain on their architecture. Also there would be ARM based ICs with integrated WiFi available. Since I, however, don't think @sphawes meant he would switch to a full fledged ARM SBC running Linux/OpenPNP on the machine itself, you would require cables for the webcams nevertheless and WiFi at the PC level would enable far greater control without messing with RF on a somewhat noisy Board controlling motors.

plasticuser, 2020-06-28:
I checked with the manufacturer (WCD) and they say they're pushing out updated drivers before the release of the next edition of Mac OS X. They will be fully 64-bit and use the new kext signing scheme.

Closed 2020-06-25.

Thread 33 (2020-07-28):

[CAD] - Front_left_leg added ramps endswitch holes and slot

Arthur-Silveira, 2020-07-28:
Added holes and slots to install the common `ramps endstop` board (mechanical endstop switch) on front left leg (Y zero switch). Based on @sphawes front left leg v 1.1.0
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

I know this board is a little more expensive than using simple endswitches, but is very common, so I think quite a few people might use it
It also has some cool leds on it, and usually comes with cables already).
I've also added some slots for PTH terminals to fit, so no need to cut them at all.
Able to use wooden screws to hold the PCB, but standard M3 thread also does the work

Had to print with supports to hold the hanging slots.
I've printed the 1st version at 100% and had to do some hammering to fit the 20x20 extrusions in place. This time I've printed with 101% size to compensate for material (PLA) shrinkage (thanks arturo for the tip). Extrusions now still fit firmly yet, with no difficulty.

I've though of adding some supports directly to the CAD file to support the recess, but I was worried about that big bridge on the original foot gap, and was going to print with supports anyway.
See some attached pictures. The total size of the recess was bigger than the board because I was thinking about some extra space for the connector to attach/detach, but in the end, the recess was so shallow that it was not necessary (maybe completely remove the PCB recess, leaving only holes and slots)

I ended on removing @sphawes original endswitch holes, but maybe a mixed solution with both options might add some flexibility on final solution.

STEP FILE attached into a zip file
[IndexPnP_1.1.0b_front-left-leg_ramps_endswitch v5.zip](https://github.com/sphawes/index/files/4989773/IndexPnP_1.1.0b_front-left-leg_ramps_endswitch.v5.zip)

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

sphawes, 2020-08-02:
Thanks for the awesome update @Arthur-Silveira! You have a really good point here, most people already have this board. Plus it's a bit cleaner to have an actual PCB to mount to the frame with a proper connector, rather than just the bare component and soldered leads. I'll be working on cad for v1.1.1 soon, ill make sure to integrate this in! Soon I'll be switching all the cad over to FreeCAD so that folks can edit the source files in Github, but in the meantime I've just been making edits myself in Fusion based on suggestions. I'll leave this open until I roll in this feature.

Arthur-Silveira, 2020-08-04:
Hey @sphawes I'm glad I could provide a little help.

Updating this issue, I had to modify one of the belt clips to improve contact to Y endswitch. It was missing the X gantry (too close to the edge), so I've added a projection to it, see attached pictures. Not it has a nice flat surface to hit.
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

Here is the clip in Fusion and step formats, if it helps
[IndexPnP_1.1.0_belt-clamp_endsw v5.zip](https://github.com/sphawes/index/files/5023962/IndexPnP_1.1.0_belt-clamp_endsw.v5.zip)

And as for the X axis endstop switch, I fixed it on top of the left gantry instead of the side. The length of the PCB matches almost perfectly. I've just applied the same holes and slots profile, and also had to reduce the top edge chamfer to put the screw holes closer to the edge (i think original chamfer was 2.5 mm, I had to reduce it to 1 mm.
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

In this case I'm not uploading the CAD file for this model because I've made another modification to it to fit different rollers (original V-slot rollers are still coming from China, and meanwhile I'm using those white rounded rollers. ). They have different dimensions, and seem to perform worse. I definitely do not recommend using them. I just did because I didn't want to wait.
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

Best regards,

daveismith, 2021-02-04:
This is in place in the free cad versions. Can this be closed?

G-Pereira, 2021-03-08:
I just tested their assembly and they are ok!

Closed 2021-03-08.

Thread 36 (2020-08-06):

[CAD] - Suggestion to improve X gantry front (increase frontal face by 2mm)

Arthur-Silveira, 2020-08-06:
I suggest, to add extra 2 mm on the frontal face of the front X gantry.

The M5x45 screw I've used to hold the rollers have a 5mm lenght head, and some of the head remains exxposed, and will interfere with the linear rail (see pictures).
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

The head top is 1.35 mm above the surface. Those extra 2 mm in the frontal face would completely cover the screw.
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

There is 3.8mm of exposed thread in the back nut (I'm using a simple nut). I know that the nylon lock nut will be a bit longer, but I think it isstill enough to spare for increasing to the front face depth.
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

This is a suggestion. If not accepted, maybe adding a warning on the BOM to use M5x45 screws with head length smaller than 3.6 mm length to avoid this issue.

OJFord, 2020-08-14:
5mm head height is per ISO4762 according to https://www.engineersedge.com/iso_socket_head_screw.htm

LoneWalkerWolf, 2020-08-15:
To those who are having the same problem:

I have made the changes to this STL File, please use this to reprint your x-gantry-front.
https://drive.google.com/file/d/1r3FPwXkL4W2Xfw1klLjvMGTdvRtRaKHC/view?usp=sharing

Thanks.

G-Pereira, 2021-01-28:
This has been incorporated to the project! Nice work!

Closed 2021-01-28.

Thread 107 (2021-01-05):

Soldermask issue

G-Pereira, 2021-01-05:
Soldermask clearance and solder mask minimum width should be set to zero in **EVERY** board. This improves solder quality for LQFP chips, otherwise solder bridges can be frequent.
Current soldermask:
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
How it should be:
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

wilhelmzeuschner, 2021-01-05:
What I believe to be the case is, that Stephen probably took this value from JLCPCB's Website: https://jlcpcb.com/capabilities/Capabilities
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

That being said, I too have always used a 0 in that setting for all of my orders (from JLCPCB) and have never experienced any issues with low-pitch packages.

bholmes451, 2021-01-05:
The other very important factor to consider is the Stencil thickness for these parts. If you are getting bridges you may need to use a thinner stencil. For a couple of my designs simply going from the default .12mm thick stencil to a .10mm stencil eliminated the bridging.

G-Pereira, 2021-01-06:
@wilhelmzeuschner that's unlikely since the set values are KiCAD defaults. KiCAD recommends setting this value to zero and the fab does the best he can.
@bholmes451 nice to know! The paste clearance and minimum width are both set to zero so this issue doesn't change the paste layer

wilhelmzeuschner, 2021-01-06:
@G-Pereira weird, when I start a new blank project these values default to 0. Maybe KiCAD remembers the last setting, although that doesn't seem to make much sense. Why would the default value be different from the recommended one anyways?

But that's not really the point, as said earlier, I completely agree with you, that this should probably be set to 0 in this case. :)

G-Pereira, 2021-01-06:
@wilhelmzeuschner That happens to me as well when I start a new project on my computer. It is always set to zero because I've changed it once to zero

Closed 2021-01-28.

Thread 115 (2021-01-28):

Fix KiCAD libraries paths

G-Pereira, 2021-01-28:

Closed 2021-01-28.

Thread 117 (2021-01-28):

[CAD] - add a tensioning screw to the Z-Side of the Y-gantry.

cad435, 2021-01-28:
Right now the tension is only applied from one side, that will bend the lower V-slot wheel. Step-file attached (please note that the attached step file is also thinner, as I modified this for my personal needs!)
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
[Issue output v1.zip](https://github.com/sphawes/index/files/5888909/Issue.output.v1.zip)

G-Pereira, 2021-01-30:
This is rather a dirty fix cad435! :D Do you have any other suggestion to this? (most probably with changes to the Z rail)

cad435, 2021-01-30:
Actually no.
This is placed so it does not interfere with anything and the screw is aligned so.it would make contact with the bolt over the whole slot.

I use this technique often, But I'm open to other approaches!

vysocan, 2021-03-13:
Hi @cad435, when I open your file in FreeCAD, I see a bit crippled, that is with mission holes and slots for M5 nuts. Please, any idea what do I do wrong?

cad435, 2021-03-13:
Just opened FreeCAD and loaded the step into it:
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
Can you please make a picture how its looking for you? What exactly do You mean with "a bit crippled"?

vysocan, 2021-03-14:
I have linux FreeCAD 0.18.4:
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

cad435, 2021-03-14:
Ah wait, you talking about the covered holes?

Yes, that's intentional. Look at the placement of the plugs, it is where the Cylindrical diameter gets smaller. That way a 3D printer would print one solid layer and the small diameter on top of that layer. After printing you can just bore it out.

It usually comes out way cleaner than without

vysocan, 2021-03-14:
OK, thank you for clarifying. I've sliced it, to see it's truly just one layer. Just misunderstand the purpose. I thought I can drill it anyway, but also thought I can ask.
Thanks Adam.

cad435, 2021-03-14:
No problem :)

vysocan, 2021-03-17:
@cad435 I've printed it out. Wondering how to insert the 3rd spacer?

cad435, 2021-03-17:
wait, I just realized that this is the X-Gantry, not the Y-Gantry...

well, yeah than you unfortunately can't use it...

vysocan, 2021-03-18:
OK, then how about making it actually thicker? That would allow the tension screw to be hidden in the body.

vysocan, 2021-03-20:
@cad435 I wonder something like this would work, and print?
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
My CAD knowledge is really on beginning.

cad435, 2021-03-20:
I would make a 0 shaped lip around that tension screw instead of making the whole part thicker.

This acts like a standoff and a printed 1mm spacer can be used so the V-Slot wheel can rotate freely...

If I manage to do this real quick this afternoon I'll post it

vysocan, 2021-03-20:
I did not make it thicker actually. I just used the original part, and applied your tension mechanism.

cad435, 2021-03-20:
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
What do you think about that? The orange part is a seperate printed part...

@G-Pereira is this worked on or still open?

G-Pereira, 2021-03-21:
@cad435 Still open, we don't have anyone looking at it yet because we are yet to finish fixing the CAD

vysocan, 2021-03-21:
@cad435 Looks fine to me. Is the part still thinner like your original one?
I've tried to finish my design as well, but having problem talk FreeCad into correctly create nut pocket :(.

cad435, 2021-03-21:
errm, yes this is thiner, because I have an lasercut acrylic part laying on top of it^^

vysocan, 2021-03-23:
I see :)

G-Pereira, 2021-05-14:
Included in the upcoming CAD revision! Thank you!

vysocan, 2021-05-14:
Hello @G-Pereira, forgot to mention, I come up with following:
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
It works quite well.
Should I try to create PR or you have already some own idea.

G-Pereira, 2021-05-16:
Hello! Check the latest video! @sphawes has already solved this issue!

Closed 2021-05-14.

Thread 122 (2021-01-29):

[Mobo] Quality of life: move position of Reset and BOOT0 buttons

wilhelmzeuschner, 2021-01-29:
In order to make debugging / programming the STM32F4 easier it would be nice if the location of the two buttons (Reset & BOOT0) could be moved away from the middle of the board.
It would be much easier to access them, if they were located on the side of the PCB.
Maybe we could even use side actuated pins, so that connectors sticking up from the board don't restrict access. Also this would make blindly pressing reset (and boot0) easier when the board is mounted far away and the buttons aren't visible.

martinbogo, 2021-01-29:
Wilhelm,

Amongst the way this is dealt with in the industry ( other than moving the
buttons to the edge ) is adding a jumper pin header to allow the buttons to
be placed offboard.   There's nothing like a big, friendly, and easy to
press button placed wherever is convenient on a machine to make things work
better.  This is how the reset buttons work on things like the external
displays on 3D printers like the Creality Ender series.

-Martin

On Fri, Jan 29, 2021 at 8:16 AM Wilhelm Zeuschner <notifications@github.com>
wrote:

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

G-Pereira, 2021-01-29:
The question is: Will we ever have some sort of UI on the machine itself?

wilhelmzeuschner, 2021-01-29:
That's a good idea, since there is quite a lot of space on the mobo, the additional headers can be added in parallel to the existing buttons. But nonetheless I'd still like to have easily accessible buttons right there on the board itself.

G-Pereira, 2021-01-30:
Actually pressing the button and going through the PC to flash it at the same time is annoying. We can save on cost and board space to have just the headers so we can use jumpers or external panel buttons. I will change the title slightly and make sure this is added to mobo-rev03. Thanks, nice work!

wilhelmzeuschner, 2021-01-30:
For another project I needed this kind of flexibly as well. I opted to overlay the footprints of a 2.0mm connector and a side actuated button. The pitch of 2.0mm is smaller than the current connectors, so it would make more sense to use a 2.54mm pitch connector instead for this project. This would also have the benefit that the clearance between the pads would be slightly increased.

2.0mm with button footprint:
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

I used these parts:
[Button](https://lcsc.com/product-detail/Tactile-Switches_Yuandi-TS-1037-A10B3-D2_C499330.html)
[Connector](https://lcsc.com/product-detail/Wire-To-Board-Wire-To-Wire-Connector_BOOMELE-Boom-Precision-Elec-C64658_C64658.html)

Here is how it looks (didn't solder the parts on):
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

G-Pereira, 2021-02-15:
This has been added to Index Mobo rev03!

Closed 2021-02-15.

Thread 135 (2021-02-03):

Enhance Power distribution on the Mobo for more flexible usage

cad435, 2021-02-03:
Currently the incoming 5V from USB is not connected to anything. That means when the Mobo is only powered by USB, the MCU can't be operated.

In normal usage, this is not a problem. However with this setup, you can't make usage of Marlins PSU_CONTROL feature, which would become handy when dealing in between PnP-Jobs. Inbetween PnP-Jobs, there is no need to have the machine running. To simplify the process of getting going, the PSU_CONTROLL Feature would come in handy, as Marlin would turn on A predefined pin from an AUX-Header or a Spare MOSFET which therefore can turn on the AC Input of the 12/24V power supply.
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

This is not possible with the current power setup, as turning off the power, power to the MCU will also be cut.
At a cost of two schottky diodes that feature could be enabled. (see picture above)

A schottky diode will effectively drop the 5V at about 300mV which leaves 4.7V USB-Voltage - thats inside the spec of 4.5V minimum USB Voltage

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

It can be further discussed if power to the stacked USB-A Connector should be better connected to the same 5V-Line than the Fe1.1s

cad435, 2021-02-03:
It should be further noticed, that If we want to be absolute safe we could replace D1(and possibly D2) with a ideal Diode IC (like a LTC4376). But that would increase the BOM cost more thatn just two schottkys.

daveismith, 2021-02-03:
@cad435 - as mentioned in, I've done similar on other boards I've designed. Those boards have always been such that the USB alone could power all of the components whereas here we create two classes of 5V power (ie, always on and only on with external power).

I can see the utility for what you're wanting to do but would want to make sure we consider the following:

- clear documentation that we make no claims or guarantees about any safety from this setup and it's for convenience rather than safety.
- a review of the impact of switching off the 5V to downstream USB devices while powering the hub
- the impact on the FE1.1s circuit as it talks about the capability to re-enumerate when switching between self and usb powered modes
- if this would also be compatible with the alternate usb hub from #98

cad435, 2021-02-03:
@daveismith

1) we don't make any guarantees anyways, otherwise we have to certify the Mobo (in EU its CE certification, not sure how USA/China is handeling Certification)

2) True, but please consider that this is the same matter with the shematic now. Our FE1.1s is only connected with Data lines and GND when the mobo is plugged in with USB Only. The proper solution would be to have a USB Voltage and Current monitor and distributing the VBUS voltage to the FE and also to the Stacked USB-A Connector

3) FE1.1s can be hardwired in the same mode, as now. Stephen chose to completely ommit the VBUS-Monitoring which does come with the FE1.1s VBUSM-Pin, so its already "as worse as it can get" (Yes I know, that is a very poor argument, but thats how it is. Proper voltage and current handling could be implemented only by increasing the board components)

4) thats true, but most certainly possible, due to the fact that we are using the FE1.1s (and any possible alternate part at the absolut minimum function, no voltage monitoring, no current monitoring)

daveismith, 2021-02-03:
Some comments:
2. For the current setup if the mobo is plugged in by USB only the FE1.1s upstream port has this issue but the downstream devices won't be powered or have anything driving d+/d- since the FE1.1s won't be powered.

In terms of the switch from self to bus powered, would that cause the re-enumeration of downstream devices? If so, that would mean turning the psu on and off would make the serial connection to the stm be re-enumerated and might break the connection (or am I misunderstanding)?

cad435, 2021-02-03:
2) true! That is absolutely true, but it only shifts the problem one step back tbh... Also, I remeber, there are a ton of USB Current supervicer IC's out there, which only are switching off the 5V rail to USB devices. I can't prove this, but due to the sheer availability of those chips i can't imagine anything bad would happen to the devices...

for the switch, I just looked into the datasheet and on page 2 it says "Automatic re-enumeration when hub switches
from self-powered mode to bus-powered mode"

So, Yes, it would auto-enumerate the devices, but I honestly don't know if the MCU with marlin would be reset by that... I can test that when I got the mobo working.

But that can be solved when hard-wiring the chip to the (more konservative) self-powering state while only monitoring the USB-Voltage which goes to the Fe1.1s and the stacked USB-A (see picture)

If you want absolutely safe you can also pack an USB overcurrent-protection IC in there as well

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

G-Pereira, 2021-02-03:
> It can be further discussed if power to the stacked USB-A Connector should be better connected to the same 5V-Line than the Fe1.1s

I would like to point out that according to [Wikipedia's page on USB specification](https://en.wikipedia.org/wiki/USB) USB 2.0 is only capable of delivering 500mA. I know that some computers allow a bit more but that's out of spec. Looking at the camera's specifications each one draws 150mA, which is in total is 300mA. So 200mA is left whichever peripherals we want to power on from USB if we choose to connect the cameras.
Of course this is for this specific cameras, if we replace them with beefier ones, that is problematic.

cad435, 2021-02-03:
OK, I specifically looked it up now.

If I understand that correctly, USB spec says the, impedance on Datalines should be 90R. that means the worst thing which can happen at 3.3V D+ and -3.3V D- (Data lines have 3.3V differential voltage for USB 1.1, 400mV for USB 2.0) is 7.3mA current draw.

Given that there is at least one 15k Pull up resistor on one Dataline (must be to indicate speed) which is located on the DEVICE, we will have less current draw. I think that this will never happen, as there are specific IC's out there which will ONLY shut the VBus down when there is too much current detected.
I never heard of a problem when using them. (For example the TPS2065D)

cad435, 2021-02-04:
OK, I think found the missing piece:

Section 7.1.6.1 of the USB spec sais, that reciever input WITHOUT termination must be at least 300k!
The termination resistors must be chosen, so that the resulting impedance must be 90R.

That means, we are perfectly safe when having D- and D+ connected to an unpowered USB slave, as the only thing that can happen are about 7mA at most through the termination resistors. And those termination resistors must be spec'ed to handle that current anyway for normal USB operation and when the USB-Datalines are IDLE.

That solves two issues:
1) we know that the FE1.1s and every other HUB IC will be fine when only connected by its data lines
2) if we go the route and make the Power distribution as I propose, we can supply the stacked USB-A with the Buck converter and be sure that the USB devices attached to that connector wont be suffering when the Buck converter is off and datalins are connected. The remaining current draw from MCU and the HUB IC would not exceed 500mA through the USB connection.

I therefore would prefer to implement the power distribution from the picture of my initial posting with the diodes as schottky diodes.

daveismith, 2021-03-12:
@cad435 - With the updated USB hub design, this needs to be revisited. @G-Pereira would like to make sure that the design in the mobo-rev03 branch is correct. Please review and comment.

 The part selected is the FE1.1 ([datasheet](https://elinux.org/images/e/ee/FE11-datasheet.pdf)). I believe that the XR22414 ([datasheet](https://www.maxlinear.com/ds/xr22414.pdf)) is the appropriate alternate.

I've found the following which shows a bus-powered design of a hub using the FE1.1 along with individual port power control. That seems like more than we want to approach, but it shows that we will need to rework circuit around at least pins VBUSM and BUS_B in our design.

Changes:
- BUS_B/BUS_PWR#/36 there needs to be a weak pulldown to GND with a strong pullup that is powered only when there is external power
- VBUSM/VBUS_SENSE/35 needs to be connected to the VBUS pin so that the device can sense when USB power is connected
- +5V net should be driven by both VBUS and the output of U12 with diodes in both places to prevent back powering.
- Insert a PTC fuse between the +5V supply and the USB downstream ports to ensure that they don't draw too much power.
- OVCB1 should be connected to the output of the PTC fuse to detect if an over-current situation has been detected
- DIS_REG should be pulled up to +disable internal regulator
- VD33_OUT should be NC
- VDD5 should not be connected (maybe put an unpopulated zero ohm in case)
- VD3_IN should be connected to +3.3V
- /XRSTJ should be pulled up to +3.3V

G-Pereira, 2021-04-05:
Added to rev03 as an optional feature configurable by solder jumpers!

Closed 2021-04-05.

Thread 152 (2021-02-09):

[CAD] - Y endstop not hitting the gantry properly

wilhelmzeuschner, 2021-02-09:
# Description
The Y endstop switch does not hit the gantry (FDM-0005-02_y-gantry) very well. To fix this, I glued a small piece of plastic onto it.
To fix this issue, the limit switch would need to be moved further "into / (to the right on the images, see below)" the front left leg (FDM-0001-01_front-left-leg), so that the switch makes better contact with the gantry . An alternative could be to design part of the gantry differently, although this could make the part harder to print, depending on the changes. Maybe a special, larger belt clamp (FDM-0025-00_belt-clamp_Body_001) could be printed but this would not be ideal either, since this part may need adjusting from time to time and would thus change the exact coordinates when homing. Also this would introduce yet another special part.

## Here are some photos:

**Illustration of the issue:**
Green: makeshift extension
Red: edge of the printed part
Yellow: limit switch contact area
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

**Same image, but unedited**
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

**Other angles:**
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

JudgeBeeb, 2021-02-09:
This is already a known issue: https://github.com/sphawes/index/issues/76

G-Pereira, 2021-02-23:
Hey! Looks like you are misusing the belt clamps. Look here:
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

wilhelmzeuschner, 2021-02-23:
The problem was my use of the older design version of the clamps, which were round and also the fact, that the limit switch was angled slightly towards the gantry. This way, it never hit either of the parts reliably.

Closed 2021-02-23.

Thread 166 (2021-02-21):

[MOBO] - Reduce amount of different BOM parts

wilhelmzeuschner, 2021-02-21:
Currently many values of capacitors / resistors are used. Most of these can be changed to one common  value.
This makes the BOM neater, greatly increases the ease of assembly by hand or PNPing since fewer part feeders are necessary.

Here are some of these parts:
4.7u: replace with 1x or 2x 2.2u
1u: (used for analog decoupling, but 2.2u should work just as good)
10u tantalum: replace with a combination of "a few" 2.2u ceramics (and 10u electrolytic? probably not needed)
10u ceramics for FE1.1: replace with smaller values (2.2u)? This value might be critical though! -> use 10u electrolytic instead of 10u ceramic to remove the ceramic from the BOM?
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

1k resistors: can be completely replaced by 10k, no critical values.
470R: probably to be removed anyhow
100k: replace with 10k (used to pull down mosfet gate)
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
560R: replace with 120R (would increase the max. current drawn from the IO when _switching_ the MOSFET (27.5mA vs 6mA, probably fine though.)
4.7k: I²C pull up, 10k should work

G-Pereira, 2021-03-03:
Thanks! Most of these suggestions were applied and the number of different value resistors was greatly reduced

Closed 2021-03-03.

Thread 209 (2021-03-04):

[MOBO] - adding I2C address pads

austinscreations, 2021-03-04:
I had mentioned this on discord, and was suggested to post here. (I'm I'm doing it correctly)
With I2c being used on the project I'd imagine there might be an external port being added where people could add their own accessories, if this is the case (i haven't looked as I'm new to the project) it might be worth ensuring that ic's that are added have their address pins broken out with solder bridge pads so that the address could be changed in the event of conflicts.

NightSkySK, 2021-03-05:
I would suggest to make it in [Adafruit STEMMA](https://learn.adafruit.com/introducing-adafruit-stemma-qt/what-is-stemma) specification, which is compatible also with Grove. In this case, we should use 4 Pin JST PH 2.0mm pitch connectors footprint
[STEMMA Technical Spec](https://learn.adafruit.com/introducing-adafruit-stemma-qt/technical-specs)

G-Pereira, 2021-03-05:
@NightSkySK there will always be a handful of different connectors used by vendors. For that reason we expose i2c pin on a AUX header for general use

daveismith, 2021-03-05:
So according to [adafruit](https://learn.adafruit.com/introducing-adafruit-stemma-qt/sparkfun-qwiic) the quiic and stemmaqt are ordered the same. In fact they say:

> STEMMA QT is cross-compatible with Qwiic - STEMMA QT connector/cable is same as Qwiic. You can use STEMMA QT devices with Qwiic devices/controllers.

NightSkySK, 2021-03-05:
@daveismith There are two connector size promoted by Adafruit
STEMMA (which is also compatible with Seeed Studio Grove ) Use JST PH 2.0mm pitch connectors
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

STEMMA QT is cross-compatible with Qwiic use 4 Pin JST SH - 1.0mm pitch connectors
STEMMA QT due to its smaller size is more convenient to use on I2C sensors and devices, once STEMMA is commonly used on microcontroller boards.

daveismith, 2021-03-05:
They also suggest: https://www.sparkfun.com/products/15109 as an option to support Grove devices. The other thing to consider is that Grove isn't always I2C so you probably would need to create an adaptor to the aux header for anything else anyhow.

NightSkySK, 2021-03-05:
I've just found that there are Qwiic connectors on the schematic as J26 and J28 and SCL and SDA lines included also as part of AUX J25 and J27 at mobo-rev03 branch so it seems to be already implemented. For me, it doesn't matter to which size of the connector is going to be placed. More important for me was to not create any new standard but use something which is already well defined and commonly used in the market. I'm sorry if I created some confusion.

austinscreations, 2021-03-05:
I've only recently started following the index project, but saw some of the newer schematics on discord where IC's are being used on the I2C bus but having the address pins latched, while it's fine to do this my thought was if you leaving the option to breakout it could be worth having pads for those address pins should anyone run into conflicts later. (at the time of opening the ticket i hadn't actually looked to see if there were already breakouts on the MOBO - maybe I should have but it's not really the focus of the ticket)

daveismith, 2021-03-05:
@austinscreations - absolutely no issue with your request, it makes some sense though in discussion yesterday I suggested to @G-Pereira that we just put a jumper footprint (resistor with both pads connected by a trace which can be cut) in place to disconnect the vacuum sensor circuit as we're not 100% sure it's going to work. that way if it doesn't we can iterate externally until we get a workable solution and then bring it back on-board. I believe his plan was to make all of this circuitry a variant so that by default it wouldn't be included on builds until it's been validated.

G-Pereira, 2021-03-05:
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
Done!

Closed 2021-03-05.

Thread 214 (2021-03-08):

[CAD] - Add small hole to access camera lens fix screw

wilhelmzeuschner, 2021-03-08:
The camera's lenses have small screws on the sides that allow to fix the lenses position. When tuning the focus it would be pretty bad if the lens could vibrate into another position over time. Currently this screw is not accessible.
In an optimal configuration this screw should be accessible when the camera is mounted, making adjustments easy.

Small holes should be added to:
FDM-0000-00_down-camera-mount_Body_001
FDM-0020-00_up-camera-mount_Body_001
Keep in mind that the lens assembly can only be mounted in two rotations (0° or 180°) in respect to the PCB.

Here are some pictures. I drilled a hole to be able to access the screw.
I added the hole to the opposite side, which is not ideal since it will be blocked when the camera is mounted.
I did this because I already glued a connector onto the other side.
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

Optimal location:
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

wilhelmzeuschner, 2021-03-14:
Here's what I changed for the up camera mount. No big changes but one mounting screw would get in the way. This one screw needs to be removed when you want to access the lenses' screw. Maybe not ideal, but still better than no access at all
I just edited the step file in Fusion since I'm not experienced in FreeCAD.
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

sphawes, 2023-05-15:
Sorry for dredging up an old thread, clearing out issues! This has been fixed as of v3, thank you for filing an issue @wilhelmzeuschner!

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

Closed 2023-05-15.

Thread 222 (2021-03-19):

[Assembly Guide] -

Gruftgrabbler, 2021-03-19:
In the assembly guide for the [x-gantry](https://docs.index-machines.com/docs/mechanical-assembly/x-gantry/) instruction nr 22 tells you to use an M5x45 to connect the GT2-Idler and the Z-Axis-Roller-Spacer to the gantry.

Doing so will result in the problem that you can not mount the camera later on. Instead you **have to use a M5x30**
to make enough space for the camera holder part.

Down below you can see that with the shorter screw it fits perfectly

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

daveismith, 2021-03-20:
Updated.

Closed 2021-03-20.

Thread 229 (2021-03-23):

[CAD] - Tensioning system for X/Y/Z Belts

cad435, 2021-03-23:
In Order to get better precision, a belt tensioning system should be added. For the Y-Axis this should be added onto the front Index leg (opposite side of stepper motor)

however, as some people already printed the complete index frame (me included) I modeled a quick addon. This tensioner can be used instead of any existing belt clamp. (Intended for use on Y-Axis, NOT X-Axis!)
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

the left arrows point to two slots where two M3 nuts are inserted. Between the right blocks is a M3 screw. which has some 7x3x3 bearings onto it. A stack of M3 spacers also can be used instead of bearings.

.step an STL's attached, use it at your own risk!
[Tensioner_Fix.zip](https://github.com/sphawes/index/files/6192890/Tensioner_Fix.zip)

Edit: tension the belt, then
move the axis and only after moving check the tensioning strength of the belt!

daveismith, 2021-04-04:
@cad435, what range of motion (in mm) does the tensioner need?

cad435, 2021-04-04:
About 2-3mm will do... More will be better, but I don't think necessary

darigovresearch, 2021-04-04:
Think this would be a great feature to add, over time belts lose their tension and having a way to do it in index would greatly reduce frustration after prolonged use!

darigovresearch, 2021-05-08:
Thanks @mhorsche thanks for taking a look at this, we haven't built an index yet so can't test it but as an initial release may be worth putting in a pull request depending on what the maintainers think. Do you have any photos of the part in use?

What do the maintainers/hardware builders think?

daveismith, 2021-05-08:
Stephen is also doing some tensioning work so hopefully between the two we
get something that works well.

On Sat, May 8, 2021 at 08:31 Darigov Research ***@***.***>
wrote:

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

MisterHW, 2021-05-16:
Exciting work! I'll leave my tensioning approach here for entertainment and inspiration. It certainly uses a minimal amount of fasteners, but it's only practical with custom sheet metal work in a certain volume.

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

https://hackaday.io/page/7198-hose-clamp-style-gt2-belt-tensioners

(timing belt crimp clamps are available, so please ignore the heat shrink tube)

maghostmil, 2021-05-24:
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

Can you add this .zip file again? It looks like expired - 404 Not found.

cad435, 2021-05-24:
@maghostmil

[Tensioner.zip](https://github.com/index-machines/index/files/6532076/Tensioner.zip)

I'll close this issue now, as this is resolved by @sphawes in https://www.youtube.com/watch?v=EN0TxylB010&

maghostmil, 2021-05-24:
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

Yes, but I completed assembly of earlier version and I need only this quick addon. Thanks.

cad435, 2021-05-25:
@maghostmil errm, I did a better job with this new tensioner addon...

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

[Y_Tensioner v5.zip](https://github.com/index-machines/index/files/6539810/Y_Tensioner.v5.zip)

sorry this came a day late... its better in nearly any aspect...

maghostmil, 2021-05-25:
Thanks @cad435. In the end, the solution from first post didn't work so well for me. When the bolt was tightened more, the addon broke at the nut. Today I will test your new version of this addon.

maghostmil, 2021-05-25:
@cad435 , I've tested this v5 addon, and works better than previous version, but I have one question for you: Wouldn't a 5mm hole be better (like hole in idler)? I feel micro-vibrations caused by idler isn't properly in whole hole.

cad435, 2021-05-25:
Well, I had only 3mm bore Idlers on hand, so I made it a M3 Bolt without any hesitation...

I may just forgotten, that the Index uses 5mm bore Idlers tbt.

But you can modify it (it's a .step, so any CAD will work) or drill out the hole...
I might do it tomorrow if I don't forget it till then :)

Closed 2021-05-24.

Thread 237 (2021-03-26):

Feeder TT Motor Mount Does Not Fit

sphawes, 2021-03-26:
In Feeder REV04 and REV05, the TT motor does not seat properly in the motor mount print. There are a few tabs on the motor that interfere, where a relief should be added to the model.

This is also just for this one specific TT motor, of which there are many small variants. Also considering what dimensions of a TT style motor are standard across brands would be good to use as the mating features of the motor mount, to allow compatibility with the most number of motors.

daveismith, 2021-03-30:
I would agree and note that even with the tab removed the current design causes issues because the motor isn't completely supported so clamping from the top can actually make the motor body come out of parallel with the PCB quite easily. I would suggest a cutout for the tab and a step up to match the difference between case size of the motor and gear box.

G-Pereira, 2021-05-04:
Does this require changes bon the PCB?

daveismith, 2021-05-04:
@G-Pereira, no. The change is in the plastics

G-Pereira, 2022-03-05:
The feeder-topology branch adresses this but it is still not ready to merge because there's topology errors in many of the files

sphawes, 2022-05-11:
Revamping all feeder files where this will be addressed, closing.

Closed 2022-05-11.

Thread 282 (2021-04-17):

Idler pulleys - stopping the rotating surface rubbing when mounted horizontally.

spavinm, 2021-04-17:
Mounting the idler pulleys horizontal causes the rotating pully wall to run on the surface of the fixing. This proposed change applies to FDM_0001_00_front_left_leg, FDM_0002_00_front_right_leg and FDM_0013_00_idler_mount.

As the inner race of the proposed/designed in idler pulleys is recessed into the part or at best flush, a boss is required to lift the rotating surface clear of the lower surface of the fixing. The current left and right front legs have approx 1.5mm (now measured) clearance on the pully, the two proposed bosses (one top and one bottom) should be added to all three parts. The boss dimensions are 0.65mm high and the flat top surface 0.5mm wide. No increase in the clearance is required.

[FDM_0001_00_front_left_leg-plus-idler-bearers.pdf](https://github.com/index-machines/index/files/6329593/FDM_0001_00_front_left_leg-plus-idler-bearers.pdf)

ocouch, 2021-04-20:
Also see relevant conversation in Discord:
https://discord.com/channels/688723670461448225/739250421893300264/832992708955078696

spavinm, 2021-04-20:
Here is picture of a modified FDM-0013-00 and the idler pully is now clear of the surface and rotates freely.
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

stuartpittaway, 2021-07-02:
Is this bug still relevant given the latest design with tensioner ?

G-Pereira, 2021-07-03:
> Is this bug still relevant given the latest design with tensioner ?

It is, nothing keeps the idler from rubbing on the print

stuartpittaway, 2021-07-03:
> > Is this bug still relevant given the latest design with tensioner ?
>
> It is, nothing keeps the idler from rubbing on the print

Ah, I used a metal washer to stop that, although I also found that the pully actually centres itself in the hole and doesn't actually touch the sides when the belt is under tension.

sphawes, 2021-09-20:
I've found the same as Stuart here. Going to close this unless someone experiences a specific problem with this.

Closed 2021-09-20.

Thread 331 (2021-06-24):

[CAD] - FDM11 X gantry M3 nut holes too small

stuartpittaway, 2021-06-24:
On FDM0011 X Gantry, the M3 nut holes are too small.

The M3 nuts are drawn inside a 5.75mm circle, the distance between flats is 4.97mm

According to this https://www.engineersedge.com/hardware/standard_metric_hex_nuts_13728.htm

The flats should be between 5.32 and 5.50mm.

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

I've 3d printed this part and can confirm the holes are very tight - I've managed to damage a couple of them and now have an M3 bolt stuck with a spinning nut inside the 3d part!

Increasing the hole diamter to 6.25mm appears to fix the issue, although I would recommend using the pocket hole feature of FreeCad to place an M3 part.

sphawes, 2021-10-05:
This fix was merged, closing.

Closed 2021-10-05.

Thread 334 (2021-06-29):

[CAD] - FDM_0011 / 0012 - poor access to tension screws

stuartpittaway, 2021-06-29:
Whilst the design of FDM11 is clever and allows the idler pully to be fitted, once it is assembled, you can no longer adjust the tension on the gantry without dismantling most of the Z parts.

In addition, the captured nut on part FDM12 has the same problem where the camera obscures access.

I have found that it is difficult to get the tension correct first time, so after a period of run in the machine gets loose and needs tightening, this is difficult as most of the Z parts/camera have to be removed.

As drawn, the slot for the V wheel is almost at its full extent of travel, which limits the possible adjustment.

sphawes, 2021-09-20:
@stuartpittaway I totally agree. A thought I've been having about the X gantry is increasing the roller count to four. This does a couple things:
- adds a bit more stability to the X gantry, preventing rotation about the x axis
- if the two bottom rollers are placed directly beneath the top rollers, there's plenty of space in the middle of the part to mount the z idler without collision

if this is something you'd like to tackle, go for it! if not, I'll take a crack at it.

stuartpittaway, 2021-09-20:
Not so sure about the 4 rollers to be honest, seems like a lot of 3d printers have moved away from that design.

How about turning the whole thing upside down? One wheel at the top? So you tension the top when instead?

I seem to get twist of the X carriage in the Y plane unless the wheels are really tight.

stuartpittaway, 2021-09-20:
If you went with 4 wheels could the bottom 2 pivot in the middle, otherwise trying to get tension equal across both is likely to lead to uneven loading and squiffy angles.

I'm not a mechanical engineer though!

stuartpittaway, 2021-09-22:
I've had a play with adding a 4th wheel.

I've added a new piece between the front and back gantry pieces - sort of "H" shaped on its side.

I've not printed out the parts yet, and lots more tinkering to do.

Let me know your thoughts.

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

Closed 2022-03-09.

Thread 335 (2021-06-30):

[BOM] - mobo-rev3 branch Ring Light BOM error (or wrong footprint)

arturo182, 2021-06-30:
In the `mobo-rev3` branch the Ring Light BOM specifies the LCSC parts for the connector to be C146126 and C141812, which are 2.54mm and 2.50mm pitch respectively, however, the connector footprint is 2.00mm pitch.

Reference: https://github.com/index-machines/index/blob/mobo-rev03/pnp/pcb/ringLight/export/ringLight-bom.csv

The footprint specifies this connector: https://lcsc.com/product-detail/Wire-To-Board-Wire-To-Wire-Connector_JST-Sales-America-B3B-PH-SM4-TBT-LF-SN_C265082.html which, upon closer inspection, can't be the correct one because of the way the ring light mounts into the assembly:

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

It has to be a side entry connector, not top entry. If I'm correct, that would mean it should be this connector: https://lcsc.com/product-detail/Wire-To-Board-Wire-To-Wire-Connector_JST-Sales-America-S3B-PH-SM4-TB-LF-SN_C265101.html

On the other (third?) hand, is the pitch of the footprint correct? I wonder because on the mobo side the connector is a 2.50mm pitch XH-series.

I understand that it's a WIP branch so those values might be in there as a placeholder "like this, but not exactly", but I thought it might be good to have an Issue for this anyway, just so it's fixed eventually.

G-Pereira, 2021-07-01:
Thank you for pointing this out! I have both these connectors on order and I will check if they fit both the PCB and the print and decide what we'll do :)

arturo182, 2021-07-01:
Sorry, I wrote the pitch for C141812 wrong, it's 2.50mm, so neither of the two will fit the 2.00mm pitch, but if you have them in post then yes, good to validate 100%

stuartpittaway, 2021-07-02:
My LCSC delivery has already arrived with the parts in it - but looks like I didn't order the connectors for the ring light!

As a work around, it should be easy to solder wires directly to the ring light board.

G-Pereira, 2021-07-03:
@stuartpittaway I would say that is possible but you are risking tearing the pad from the PCB

daveismith, 2021-07-03:
You may want to use some hot glue and a zip tie to provide some strain
relief if you do that.

On Sat, Jul 3, 2021 at 06:58 Gonçalo Pereira ***@***.***>
wrote:

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

arturo182, 2021-07-12:
I have now received the side entry connector https://lcsc.com/product-detail/Wire-To-Board-Wire-To-Wire-Connector_JST-Sales-America-S3B-PH-SM4-TB-LF-SN_C265101.html and can confirm it does work with the case but doesn't match the footprint on the PCB. I mean, you can force it if you want it, but it's clearly a top-entry footprint:

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

G-Pereira, 2021-07-28:
Confirmed this is not an issue.

arturo182, 2021-07-29:
Can you expand, cause the footprint doesn't match the part specified 😅

G-Pereira, 2021-07-30:
Right, although it is not an issue I will keep this open to denote the change

G-Pereira, 2021-09-10:
This has been fixed by changing the connector to a XH through hole!

Closed 2021-09-10.

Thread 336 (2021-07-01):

[MOBO] - Move to on-board stepper drivers (TMC2209)

G-Pereira, 2021-07-01:
**Motherboard Revision:** REV04

**Enhancement Description:**
- Move to on board drivers being TMC2209 or better at the date of this enhancement.

stuartpittaway, 2021-07-07:
Is this change to put soldered on TMC drivers on the mobo ?

daveismith, 2021-07-08:
I think that's what's being proposed. It won't be happening until mobo rev3 is released (ie, even if there needs to be corrections to rev 3 it won't include moving to onboard drivers).

I'm unsure what to think of moving this way, but would note that it will need some significant work on the heat dissipation and EMI aspects of the layout.

stuartpittaway, 2021-07-08:
Having burnt out a few driver chips in the past, a pluggable design works best in my mind.

Additionally when new chips are released, they could be used without changes

plasticuser, 2021-07-08:
I avoidf buying boards where the controller is built in. They're a pig to repair quickly in a production environment, where as driver boards of the standard fit are a quick swap. This makes fault diagnosis really quick and easy.

I'm also not keen on the idea of being locked into a specific driver. Mid-scale has a large "at home" component, and the newer generation of silent drivers are really attractive to people like me.

My $0.02.

G-Pereira, 2021-07-14:
This change is aimed at the moment we can look at the index electronics as a black box. You generally don't swap drivers on your washing machine or any other home appliances just like you won't on a final product.

For this to be true a careful design has to be made like @daveismith suggested and some headrooms and protections need to be in place. This won't make sense during prototyping for sure.

I didn't always had this opinion but other people helped me realize that.

daveismith, 2021-07-14:
It would be interesting to do a cost calculation to see if there is much savings in BOM cost by going with the on board drivers. I would tend to agree with the sentiments of @stuartpittaway and @plasticuser that from a repairability perspective, the modules are better. If they aren't significantly more in terms of cost, it's probably worthwhile keeping modules. If the concern is soldering the headers for the modules, then we could look at SMT headers so they can be reflowed

G-Pereira, 2021-07-14:
My experience has been a little different. My 3d printer always was a self made machine and the one of the reasons I've burnt stepper drivers was when I was setting their current limit really high so I could cover up unrelated mechanical issues on my machine when I lacked experience on the subject overheating the drivers considetably. The other reason was connecting the stepper drivers reversed by mistake.

None of this reasons were a lifespan issue about the drivers and I am pretty confident that most failures people have with drivers is using them out of spec, overheating them.
Trinamic drivers aren't low quality drivers so they don't simply fail since they have several protection mechanisms. I am aware of people burning Trinamic drivers is common on TMC2130 since they have a high RDsOn which makes people overheating them most of the times.

In the Index context, contrary to "universal" 3d printer boards, we have a clear notion of what hardware we will interact with this we can design accordingly. And keep in mind that this won't impose limitations to custom setups because TMC2209 has an high current specification (2A).

EngelenH-kpn, 2021-07-29:
Which begs the question, and that is all it is, should you go for a black box design?

For the steppers, I see no benefit at all in making them onboard. Maybe I am missing it. Even if you design the board for just the Index hardware, accidents happen. Also, given the target audience for this device, I think I can say with some certainty that this audience will have a bin full of the plug-in stepper drivers on their desk right now.

On a larger whole, and this is a question more for me, would it not be an idea to build the board as a 'universal' board? Or at least to some extent. Yes it would be mainly for the 'index' hardware but as you already indicated. People will quickly start making custom setups, might as well embrace them into the community too. For instance I recently scored a TVM802 cheap, could see myself using this board for that machine too.

bholmes451, 2021-07-29:
I believe there are plenty of "Universal" boards on the market already (I have several). Some have stayed the course and are still around and other have not. I agree with @G-Pereira on this. There is not much advantage in going universal for this simply because we know the hardware targeted (Pick and Place machines). If you are looking at using something outside the design, then perhaps a different board would be better. At most, I would agree to split out the Step/Dir pins for each stepper driver so you could send them to a separate, not on board, system. I do this sometimes, to add industrial servo motors to my design.

daveismith, 2021-07-29:
Didn’t we land on the approach to this ticket being a review to see if it
would be possible to handle both and a user can choose which to populate.

In terms of headers, you can absolute get SMT headers which the drivers
could use so I don’t think the argument of putting down the driver itself
being the only way to get to fully SMT applies (also we have USB ports and
the power terminal block which shouldn’t go SMT for mechanical reasons).

Having said that, putting the driver on board would reduce component count
and likely make the overall solution cheaper.

On Thu, Jul 29, 2021 at 12:17 Gonçalo Pereira ***@***.***>
wrote:

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

G-Pereira, 2021-07-30:
This is something we have to discuss yes. I am just answering "what advantages would it have"

EngelenH-kpn, 2021-07-30:
I guess from my end, but it is not my project so if this is the case so be it, I am surprised or perhaps more accurately disappointed the mission goal for this project (or at least the controller board) has changed. That was one of the reasons why I took notice of the project over a year ago.

If the costs are not much reduced as you say, we are left with just the complete assembly by JLCPCB. Which also touches upon one other reason for me personally to be weary of this black box approach you spoke of. I have the displeasure of living in a region where availability the components (mechanical and electronic) are just a pain and import fees are oppressive (especially for China products, yes that fun EU law that went into effect on July 1). So for me it will have to be a case of 'use what I can find easily and often locally'.

plasticuser, 2021-07-30:
The mission statement of the Index placer is to have a machine that is affordable for the common person. Affordability isn't just the initial price. It's also the build quality, the future maintainability and overall reliability of the board, and the death of the board when it is no longer serviceable or has been superseded by a better model.

While I'd *prefer* plug in steppers so I can use the board with a wide variety of systems and have it available and useful to most of the OpenPnP community, I also will buy it anyway if only to have an official unit to test against.

The thing about machines designed by committee is we don't all get everything we want. So if the drivers are built in, I will still get one. I'd just prefer they're not, for a multitude of reasons.

EngelenH-kpn, 2021-08-02:
I agree except the 'universal' aspect, for clarity, was one of the original goals of Stephen. In fact his video as to that effect comes up (at least for me, not sure if this is just for me or not) at the top of the list when I google 'universal openpnp controller'.

So I am not questioning the change discussed here because I want to change the direction of the project and steer it towards 'universal' either personally or 'by committee' but because this change seems to conflict with what Stephen set out to do. On top of that I think he had the right idea.

Possibly however this goal has changed and I am just not aware of it.

G-Pereira, 2021-08-08:
@EngelenH-kpn that's correct, we need to discuss this more through because of that. At the moment we are excited to make the machine do what it was designed to and it is starting to show real and awesome results so this is definitely at the bottom of our priorities. I think Rev03 has been showing great results and it will be here for a while!

feldon30, 2021-08-28:
Stepper driver ICs are known for burning out. The target audience of Index PnP is not pure Consumers but Makers who would be more than comfortable replacing a module but may hesitate at floating and replacing a QFN-28 on a densely populated 4-layer board. I believe Modules would give us a bump in Repairability.

A4988 modules seem to be about $2 each.
TMC2209 modules seem to run $4.50-6 each.
TMC2209 bare chip are currently unavailable DK and Mouser, while Newark has some for $3 each. With the addition of trim pots and other support hardware, the price difference at this scale may be a wash when comparing integrated vs. module.

plasticuser, 2021-08-28:
Using modules allows us to take advantage of future stepper driver models
instead of locking us in to a specific part.

It makes it trivially repairable.

It makes it reconfigurable to future needs, experimenting and future Index
development.

Using SMD mounted components deprives us of all these

MrPix

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

lucian151, 2021-09-08:
Should we label this "wont fix"? Seems like the plan after a lot of discussion here.

EngelenH-kpn, 2021-09-09:
Alternatively you could support both options, put the footprints for both on the board so you can either use an integrated stepper driver or solder in headers for a module. Maybe even add something like screw terminals or a connector to hook into an external stepper driver module. It would satisfy all groups but cost space on the board.

G-Pereira, 2021-09-12:
@lucian151 I think this could be revisited once we line our ideas for rev04

sphawes, 2021-09-20:
Going to close this. I agree something definitely to be revisited, but if it becomes an obvious improvement down the road, we'll make a new issue for it then! :D

Closed 2021-09-20.

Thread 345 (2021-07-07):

[MOBO] - Polarity Protection P-mosfet current limit/Thermals

EdHayes3, 2021-07-07:
**Motherboard Revision:**
REV003

**Issue Description:**
- Polarity protection P-mosfet is pretty close to it's current limit. If each stepper motor is at 1.7a, you are at 6.8amps. P mosfet is rated at 8.8A, and assumes you are using a 1 in^2 pad, with 2oz copper.  With all the other stuff on the board, I'm thinking you may want some additional current headroom and/or thermal management here.
- Obviously, rarely everything will be consuming power at all times, I'd still try and go a bit higher if you can.
- Pulsed current is higher, but assumes duty cycle ≤ 2%; not sure if this applies.

**Suggested Fix:**
- Alternate part (IRF9321TRPbF*, AO4407A, HY12P03S*, NCE30P25S*) [I did not spend too much time looking for alternatives]
- Watch gate-source voltage on any replacement if using 24v power supply.

G-Pereira, 2021-07-14:
We have designed to configure motors at 1A so there's more or less 1.5A also considering the remaining power consumption. I agree that's hard to guarantee without having a specific type of drivers allowed with a specific provided configuration file that limits current. We don't want to have this for now so people can prototype the machine easily at the moment with any driver they have at hand.
This will change in rev04 and a more formal design can be established.

theacodes, 2023-05-01:
This has been resolved in rev4, as far as I can tell.

Closed 2023-05-01.

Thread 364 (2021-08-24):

[MOBO] - REV003 BOM Missing PN for Motor Driver Sockets

Phase4logic, 2021-08-24:
REV003 - Motor Driver Sockets missing from BOM

I'm not seeing an entry in the BOM for the Motor Driver sockets (A1-A6).  I can see that they are 8 pin sockets with 2.54cm spacing, but I don't know how tall they need to be to clear the capacitor and any pins sticking down from the driver board.  Could someone respond to me with a part # or specs?

Thanks!
Mark

feldon30, 2021-08-31:
There's actually an entry in the BOM for these that says Pololu_Breakout-16_15.2x20.3mm which is a standardized stepper driver footprint used in CNC, 3D printers, and other applications that use stepper driver modules. However the note field in the BOM next to the Pololu Breakout suggests A4988 stepper drivers which are the most basic steppers you can get ($1-2/ea). According to several comments in Discord, the preferred stepper driver for the Index is the much upgraded TMC2209 ($4.50-6/ea). If I were you I'd wait for the next revision before ordering any parts.

Phase4logic, 2021-08-31:
Actually I was looking for a part number for the sockets that are soldered
onto the board that the driver you are referring to plugs into.

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

feldon30, 2021-08-31:
It's 2.54mm straight socket female pin header.

Phase4logic, 2021-08-31:
Do you happen to have a minimum vertical height so that the driver board clears the capacitor under it?  These sockets should be in the BOM.

Mark

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

daveismith, 2021-08-31:
You can use LCSC part [C429957](https://lcsc.com/product-detail/Pin-Header-Female-Header_JILN-22850108ANG1SYA01_C429957.html). I wasn't sure how to put it into the BOM because it's a single footprint but you need to order two of this part for each footprint.

Phase4logic, 2021-08-31:
Thanks David. One approach would be to make the socket the BOM item, which would split the footprint into two parts. (I’m not sure how to do that) Then the next-level-up BOM would have the PCB, the motor drivers and any other items that plug into the board.

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

G-Pereira, 2021-09-02:
I was aware of this but I still haven't found a clean way to assign that part number to the PCB. I am avoiding using two separate footprints for the driver headers since that is easily messed up while working on the layout.

Let's keep this issue open until this is sorted out or maybe receive suggestions from anyone.

solarmax1, 2022-03-20:
I happened upon an article that discusses how to handle this in KiCad. The examples they give are the opposite of this case, but I think you will get the idea.   Wow, I just noticed this article is from 10 years ago!  Hope it still works.
https://kicad-users.yahoogroups.narkive.com/NXR3fWfE/managing-multi-part-components-ic-socket-battery-socket-into-bom

theacodes, 2022-06-19:
KiCAD 6 allows items on the schematic (and therefore BOM) to be excluded from the PCB. We can use this to note the MPN for the sockets.

Closed 2023-05-12.

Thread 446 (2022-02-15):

Assembly.FSCad has references to files which have been renamed/don't exist

stuartpittaway, 2022-02-15:
If you trigger the generate "part list" function in FreeCad, it reports lots of errors of files which no longer exist/renamed.

```
08:46:58  fcDocumentReader: file E:\source\index\pnp\cad\OTS\MakerBot LimitSwitchBoard.STEP does not exist!
08:46:58  fcDocumentReader: file E:\source\index\pnp\cad\OTS\OTS-0009_20x20_v_slot_600mm.step does not exist!
08:46:58  fcDocumentReader: file E:\source\Downloads\v-slot-roller.step does not exist!
08:46:58  fcDocumentReader: file E:\source\index\pnp\cad\OTS\v-slot-roller.step does not exist!
08:46:58  fcDocumentReader: file E:\source\index\pnp\cad\OTS\M5-tslot-nut.step does not exist!
08:46:58  fcDocumentReader: file E:\source\index\pnp\cad\FDM\front-leg-tensioner.FCStd does not exist!
08:46:58  fcDocumentReader: file E:\source\index\pnp\cad\OTS\Nema 17 42A02C v2.step does not exist!
08:46:58  fcDocumentReader: file E:\source\index\pnp\cad\OTS\Gates_2GT_20T_Toothed_Pulley.STEP does not exist!
08:46:58  fcDocumentReader: file E:\source\index\pnp\cad\OTS\Gates_2GT_20T_Toothed_Idler.STEP does not exist!
08:46:58  fcDocumentReader: file E:\source\index\pnp\cad\OTS\94000A330_18-8 STAINLESS STEEL CAP NUT.STEP does not exist!
08:46:58  fcDocumentReader: file E:\source\index\pnp\cad\OTS\Linear Rail &amp; Block LML9B v3.step does not exist!
08:46:58  fcDocumentReader: file E:\source\index\pnp\cad\OTS\MS4M-M5.STEP does not exist!
08:46:58  fcDocumentReader: file E:\source\index\pnp\cad\OTS\smc_stepper.stp does not exist!
08:46:58  fcDocumentReader: file E:\source\index\pnp\cad\OTS\OTS-0011_v-slot-roller.step is no FCStd file!
08:46:58  fcDocumentReader: file \home\stephen\index\pnp\cad\FDM\FDM-0037_belt-tension-arm.FCStd does not exist!
08:46:58  fcDocumentReader: file E:\source\index\pnp\cad\OTS\2020CornerBracket.step does not exist!
08:46:58  fcDocumentReader: file E:\source\index\pnp\cad\FDM\FDM-0045_corner_bracket.FCStd does not exist!
08:46:58  fcDocumentReader: file E:\source\index\pnp\cad\OTS\URY6M-4M.STEP does not exist!
08:46:58  fcDocumentReader: file E:\source\index\pnp\cad\PCB\PCB-0001-00_index_motherboard.step is no FCStd file!
08:46:58  #PARTSLIST# spreadsheet has been created
```

stuartpittaway, 2022-02-16:
@sphawes I've remapped the 3d models/parts in assembly to the correct filenames in the FDM/OTS/FST folders etc.

I've also added the model "94000A330_18-8 STAINLESS STEEL CAP NUT.STEP" into the FST folder as it was missing - this needs to be renamed to "FST-XXXX" - I'm not sure how you are numbering these parts, is this something you can pick up and then correct the assembly model?

Also updated the BOM generation script, which now outputs the below.  The ordering has changed to filename + description, which I think makes more sense.

Seems to be a lot of concern/comments over this BOM file.  I believe we can embed comments/data into the FreeCad model for automatic export using the "part data" feature of a2plus, but not experimented with it.

You will notice on the below that rogue filenames like "2020CornerBracket.step", "FDM-0045_corner_bracket.FCStd" and "Gates_2GT_20T_Toothed_Idler.STEP" have been corrected.

Also seems to be some confusion because this list has the full filename of the FreeCad model vs the 3d STL part number - is this something to resolve?

|Description|Supplier|Filename|Quantity|
|-----------|--------|--------|--------|
|||94000A330_18-8 STAINLESS STEEL CAP NUT.STEP|3|
|||CSM-0001_staging-plate.FCStd|1|
|DIN985 Nut M5|||7|
|||FDM-0001_front-left-leg.FCStd|1|
|||FDM-0002_front-right-leg.FCStd|1|
|||FDM-0003_back-left-leg.FCStd|1|
|||FDM-0004_back-right-leg.FCStd|1|
|||FDM-0005_y-gantry.FCStd|2|
|||FDM-0006_x-motor-mount.FCStd|1|
|||FDM-0007_frame-umbilical-mount.FCStd|1|
|||FDM-0008_y-gantry-support.FCStd|2|
|||FDM-0009_roller-spacer.FCStd|6|
|||FDM-0010_y-gantry-umbilical-mount.FCStd|1|
|||FDM-0011_x-gantry-front.FCStd|1|
|||FDM-0012_x-gantry-back.FCStd|1|
|||FDM-0013_x-idler-mount.FCStd|1|
|||FDM-0014_down-camera-mount.FCStd|1|
|||FDM-0015_down-light-mount.FCStd|1|
|||FDM-0017_z-gantry-left.FCStd|1|
|||FDM-0019_up-light-mount.FCStd|1|
|||FDM-0020_up-camera-mount.FCStd|1|
|||FDM-0021_foot.FCStd|1|
|||FDM-0022_umbilical-guide.FCStd|1|
|||FDM-0023_peek-cable-guide.FCStd|6|
|||FDM-0024_nozzle-holder.FCStd|1|
|||FDM-0025_pump-mount.FCStd|1|
|||FDM-0027_belt-clamp.FCStd|6|
|||FDM-0037_belt-tension-arm.FCStd|3|
|||FDM-0039_z-gantry-right.FCStd|1|
|||FDM-0040_z-gantry-backplate-left.FCStd|1|
|||FDM-0041_z-gantry-backplate-right.FCStd|1|
|||FDM-0042_valve-mount.FCStd|1|
|||FDM-0044_x-gantry-tension-bar.FCStd|2|
|||FDM-0046_umbilical-swivel-base.FCStd|1|
|||FDM-0047_umbilical-swivel-extension.FCStd|1|
|||FDM-0055_datum-board-mount.FCStd|1|
|||FDM-9001_squaring-bracket.FCStd|2|
|||FST-0016_M5-tslot-nut.step|34|
|ISO4032 Nut M3|||43|
|ISO4032 Nut M5|||31|
|ISO4762 Screw M2.5x20|||4|
|ISO4762 Screw M2.5x8|||8|
|ISO4762 Screw M3x16|||11|
|ISO4762 Screw M3x30|||9|
|ISO4762 Screw M5x10|||30|
|ISO4762 Screw M5x25|||14|
|ISO4762 Screw M5x40|||14|
|ISO7380-1 Screw M3x10|||18|
|ISO7380-1 Screw M3x14|||14|
|ISO7380-1 Screw M3x8|||31|
|ISO7380-1 Screw M5x8|||16|
|||OTS-0001-00_CP40-nozzle-holder.FCStd|1|
|||OTS-0002-00_usb-webcam.FCStd|2|
|||OTS-0003-00_vacuum-pump.FCStd|1|
|||OTS-0005-00_zip-tie.FCStd|6|
|||OTS-0007-00_y-gantry-shroud.FCStd|1|
|||OTS-0008-00_x-gantry-shroud.FCStd|1|
|||OTS-0009_pneumatic-splitter-URY6M-4M.STEP|1|
|||OTS-0010_20x20-v-slot-600mm.step|7|
|||OTS-0011_v-slot-roller.step|10|
|||OTS-0012_nema17-stepper.step|4|
|||OTS-0013_nema11-hollow-shaft-stepper.stp|1|
|||OTS-0014_linear-rail-100mm-LML9B.step|4|
|||OTS-0015_20x20-corner-bracket.step|6|
|||OTS-0016_GT2-20-tooth-idler.STEP|4|
|||OTS-0017_GT2-20-tooth-pulley.STEP|4|
|||OTS-0018_pneumatic-coupler-MS4M-M5.STEP|1|
|||OTS-0019_limit-switch-PCBA.STEP|3|
|||OTS-0020-00_24v_3-Way_Solenoid_Valve_0526T_www.fspump.cn.FCStd|1|
|||PCB-0001-00_index_motherboard.step|1|

Closed 2022-03-09.

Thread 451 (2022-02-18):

8mm Strip Feeder

DirtyEngineer, 2022-02-18:
There has been several requests for a 8mm version of the strip feeder. The parametric file has several issues with the 8mm value. The male tabs are 8mm to long and the 3 relief holes are 4mm from were they should be. I sorted those out and exported the STL's for the strip feeder and cover which are attached. I have not printed these so please use at your own risk.

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

[8mm Strip Feeder and Cover STL.zip](https://github.com/index-machines/index/files/8099309/8mm.Strip.Feeder.and.Cover.STL.zip)

Also included is the FreeCAD part. You will need to set the correct path to the "RobotoMono" font from the Lumen repo. Do not try to use this file for the other strip sizes as the formulas are not correct.

[FDM-9002_8mm.zip](https://github.com/index-machines/index/files/8099355/FDM-9002_8mm.zip)

mbike2000ru, 2022-02-19:
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
Hello,
I made a 8 mm smd feeder guides and a cap just to keep smd components after work. But I did it in Fusion360.
I can give my STL if needed.
I attach it to the mounting plate simply by squzing by 4 clamps. It allows to use other sizes of feeders.

stuartpittaway, 2022-02-21:
@G-Pereira can you with the existing parametric strip feeder?  Seems like a lot of people are having issues after the "keeper" was added.

stuartpittaway, 2022-02-21:
@DirtyEngineer just to clarify, you have taken a look at the "StripFeederParams" spreadsheet in FreeCad and tweaked the values (the ones which state "ONLY CHANGE THIS!").

You can set "TapeWidth" to 8mm and "NumberOfHolders" to the required value (8)

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

This should then produce this file.  You may need to tweak the font file/path on the "Cover_Label" and "SMD_Material" objects.

The tabs should have a hole in them as well, they are designed to allow multiple strip feeders to be placed next to each other without requiring gaps/taking up extra space.  They can also be disabled by changing the parameter "EnableTab" (although looks like this has some issues at the moment)

I would also recommend printing this piece flat on its base - the version in releases appears to be set vertically.

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

G-Pereira, 2022-02-21:
Thank you! I'll review this in the next day or two. I have a bunch of these printed and can better see what is going on.

InfiniteNesLives, 2022-02-23:
Stephen shared the one he's currently using on discord.

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

[FDM-0048_8mm-strip-feeder.zip](https://github.com/index-machines/index/files/8125289/FDM-0048_8mm-strip-feeder.zip)

DirtyEngineer, 2022-02-25:
Seems this isn't really an issue. The model has the clearance holes placed so they align with screw heads on the staging plate.  The tabs are zero thickness so they don't print so that issue isn't a problem.

Attached is an 8mm x 7 lane STL as this seems to be a common requested size.
[FDM-9002_8mm_x7.zip](https://github.com/index-machines/index/files/8142478/FDM-9002_8mm_x7.zip)

G-Pereira, 2022-03-06:
@MakeItHackin @InfiniteNesLives and @mbike2000ru The parametric strip feeder is meant to be flexible with every user preferences. Keep in mind that that feeder Stephen shared only allows resistors and capacitors and there's some components that use 8mm tape and the pockets are a little deep

Closed 2022-02-25.

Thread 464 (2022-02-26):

parts.csv, INDES BOM - MECH.csv & index_bom.md inconsistent, Which to use

Typhoor, 2022-02-26:
Please fill out the following:
- Build Number where this issue is present. (This is the same as the most recent tag number): v2.0.1
- Is this recording an active issue, or suggesting an improvement?: active issue
- Are you just logging an issue, or do you have a solution in mind?: no solution -> question

the three files are inconsistant; which is the master one, which to take ?
i.e. INDEX BOM - MECH.csv & parts.csv both show part `FDM-0026 board-holder`:
but I do not find CAD or STL files in release or on git ?!?

sphawes, 2022-03-01:
Hey @Typhoor! Thanks for the note!

The `parts.csv` file is a master list of every part number in the project. You can read about it on the Contributing page of the wiki: https://github.com/index-machines/index/wiki/Contributing#part-numbers.

'INDEX BOM - MECH.csv' is a file meant to help folks source parts if they're building their own machine from scratch.

`index_bom.md` is automatically generated from the CAD assembly, is unique to each tagged release, and is used for folks building their kit. You can read a bit more about it on the docs page: https://docs.opulo.io/docs/

I agree that these three can be confusing, and it's not clear what each one of them does at first glance. I'll rename them so that it's a bit more intuitive! Thanks for the feedback!

Typhoor, 2022-03-01:
Thanks for the explanation, actually I understood this.
Question was what is the Master, which to follow if there is inconsistency?
and ...
Where do I find CAD or 3d-files for FDM-0026 ?
Was this part abandoned ? Or replaced with a new part ? What to use as a `board-holder`

stuartpittaway, 2022-03-02:
FDM-0026 no longer exists.

You mention board-holder, do you mean to mount the mobo PCB to the plate or to hold the work piece PCB for assembly?

FDM-9000_motherboard-mount or FDM-9007_pcb_holder_rightangle perform this function respectively.  You would need to print multiple to suit your application.

The official kits use metal standoffs instead of FDM-9000.

There is also on going work to improve the BOM, to obtain a single file, experimental version can be found here https://github.com/index-machines/index/blob/cad-staging/pnp/cad/index_bom.md

stuartpittaway, 2022-03-09:
@Typhoor can this now be closed, the latest index_bom.md file has become the single source for BOM information.

Closed 2022-03-09.

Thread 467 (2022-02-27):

Default homing steps re-order

InfiniteNesLives, 2022-02-27:
I suggest the X/Y axis' be homed first, then Z.  Changing the default HOME_COMMAND in the openpnp config to the following:
```
G28 XY; Home X and Y axes
G28 Z; Home Z axis
G1 Z25; raise Z nozzle
```

To me, it's a LOT safer to assume that the nozzle is currently at a safe Z height, than assuming there is adequate clearance at the current X/Y location to perform Z homing first.

The provided config homes the Z axis first which is quite likely to drive the nozzle into the staging plate, components, boards, etc.

I'd say so far, well over 95% of the time my machine is at a safe Z height, but not a safe X/Y location to perform a Z homing.  So it makes more sense to home X/Y first, and then Z.

it's also just more intuitive that if the nozzle is plunged down somewhere random it's prob not safe to home the machine.  By default the machine is usually left/powered down with a safe Z height, but not a safe Z homing location.  It's not intuitive that if you shut the machine down in a normal state, that you can't safely perform a homing procedure..

I was pretty anxious about homing the machine once I was confident enough to attach the nozzle.  Had this order been flipped, I doubt I would have driven my nozzle into the staging plate/datum board so many times...

InfiniteNesLives, 2022-02-28:
Other thing I've noticed is that the first homing after power up/reset always fails for me because the ring lights don't come on until the second before openPNP starts to analyze the downward camera looking for the homing fiducial.  So the cameras don't have enough time to react to the new light and don't produce good images for visual recognition.

Perhaps there's a better solution, but adding this step to the HOME_COMMAND resolved the issue for me, so the cameras can adjust early.

```
M150 P255 R255 U255 B255   ;turn on ring lights (need camera to start adjusting before looks for fiducial)
G28 XY; Home X and Y axes
G28 Z; Home Z axis
G1 Z25; raise Z nozzle
```

InfiniteNesLives, 2022-02-28:
Sorry for the multiple separate notes! :)

But realizing one other related item I'm curious about.  For the first homing after powerup/reset the machine raises the left nozzle prior to homing (but only on first homing after power up, not on subsequent ones).

The problem I'm foreseeing, and curious about a fix, is that this also happens to drive the right nozzle into whatever rests below.  So the first homing after powerup could also cause damage with whatever happens to be attached to the second nozzle.  IMO, the behavor of first homing after power up and all subsequent ones should be identical.  The PNP can be a risky process so the mental checklist one makes before clicking that button should always be the same regardless of how long the machine has been running.

I don't have a recommended fix for this as I'm not sure what's directing this action.  My guess is that it's baked into the firmware?  I also realize this can be seen as a feature for single head users, but it's a problem for dual head users.  So perhaps a means of toggling this feature would be best?  If my assumptions are correct that it's baked into the firmware, perhaps it should be migrated to openpnp to make it easy for the user to toggle on/off as desired.

sphawes, 2022-03-01:
Hey @InfiniteNesLives! Thank you so much for all the notes! A bit of background on why we did it the way we did:

We have our Marlin config choose to home X and Y first before Z for many of the reasons you stated in your first comment. In general, moving the Z axis when the machine position is unknown is pretty prone to collision, so we prefer to home it last where we know it won't collide with anything.

We have a setting in Marlin configured where the machine moves Z to a "safe height" before homing. On boot, it thinks its position is 0, 0, 0, so it defaults to moving Z up 32mm (or somewhere around there, i forget the exact number) before homing for safety. After it homes and knows its true position, it won't move Z up because it knows it's at the safe Z height already.

When two nozzles are attached to the head, this does become a problem. Moving the left nozzle up brings the right one down, and we're back to a collision. When we support dual head LumenPnP builds, we'll actually release a separate Marlin config that takes this into account, and will likely just keep the Z axis exactly where it is where it's still pretty unlikely we'll get a collision.

As for ensuring the lights are on before fiducial homing, I believe there's an OpenPnP setting that triggers an actuator when the machine homes, I'll make an edit that includes that (or use your GCode snippet if I'm mistaken). Thanks for all the wonderful notes! I'll close this unless you feel something is unresolved.

InfiniteNesLives, 2022-03-02:
Thanks Stephen!

Yeah so I'm now realizing that most of these problems I was having are because I was using the firmware release from current github actions: https://github.com/index-machines/index/actions/workflows/build-marlin-for-index-mobo.yml

When I update to the current tagged release: https://github.com/index-machines/index/releases/tag/v2.0.1

#1: My problem with the nozzle driving into the staging plate is resolved.  (The released firmware corrects this with a similar solution I used in openpnp as you said)

#2: My concern about the right nozzle driving down on the first homing after power up is minimized if not gone because it appears the Z axis only moves ~5mm.  So the right nozzle isn't actually driven down very far.

#3: The issue with ring lights not turning on until just before imaging the homing fiducial is still present of course.  I'm curious to hear where you find the openpnp setting if you find it just for my own learning.  But yeah, quite a minor thing in any event, I just wanted to point it out as a potential issue for other users who might be confused/annoyed as to why the first homing always fails fiducial check.

stuartpittaway, 2022-03-02:
> 3: The issue with ring lights not turning on until just before imaging the homing fiducial is still present of course. I'm curious to hear where you find the openpnp setting if you find it just for my own learning.

I've had a lot of issues with openpnp and the "async gcode driver", it doesn't appear to wait for multiple gcode commands to run/finish before moving onto the next step/movement.

Therefore, it can switch on the light and move at the same time, but often the light hasn't yet responded before the next action takes place (like the camera).

This can also be a problem with not enabling the "machine coordination" settings on the actuators.

Closed 2022-03-02.

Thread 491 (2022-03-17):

Vacuum sensing test missing step to actuate valve

InfiniteNesLives, 2022-03-17:
https://docs.opulo.io/docs/testing/actuator-check/#vacuum-sensors

The vacuum sensing test in opulo docs never instructs you to actuate (power on) the vacuum solenoid valve.  Unless I'm mistaken, this is a vital & required step to draw vacuum on the sensor.  Without powering the valve, the line is vented to atmospheric pressure.  I don't have vacuum sensing enabled on my machine so I could be wrong, but several users are reporting problems with the vacuum sensing test and I think this is probably why.

atanisoft, 2022-03-17:
I'm working on configuring OpenPnP for my projects and after importing the Opulo machine.xml (via overwrite in config directory) I found there are a couple Actuators that are defined on the GCodeDriver that don't exist:
https://github.com/index-machines/index/blob/01702144b94ddbe14eabd6cf24d7e3c43b42dba0/openpnp/machine.xml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

I haven't dug into the Marlin code to see exactly what these codes do in regard to the Opulo but I suspect this may be related to the vacuum sensing.

jellewie, 2022-03-18:
Just looked up the Gcode of @atanisoft , just here to report them:

https://marlinfw.org/docs/gcode/M042.html Set Pin State - M42 Ignore Pin State Mode
https://marlinfw.org/docs/gcode/G004.html Dwell - G4

https://marlinfw.org/docs/gcode/M106.html Set Fan Speed - M106 MaterialIndex index speed secondary

https://marlinfw.org/docs/gcode/M150.html Set RGB(W) Color  - M150 intensity pixel intensit intensity strip intensit intensity

atanisoft, 2022-03-18:
Yeah, I don't know if these actuators are important or not but they are defined on the GCodeDriver but the `head-mountable-id` value is invalid for any of the defined actuators.

stuartpittaway, 2022-03-18:
> The vacuum sensing test in opulo docs never instructs you to actuate (power on) the vacuum solenoid valve.

It may be missing from the documentation, but Stephen was using these two commands when the pump gets switched on.  This means both the pump and the valve operate together, which is how he's been running.

There were a few comments about OpenPNP not opening/closing the valve at the correct point in the pnp process if the valve was a separate actuator.  I've tried both and didn't see a problem.

"Pump Left" actuator GCODE ```ACTUATE_BOOLEAN_COMMAND```
```
{True:M106 P1}{False:M107 P1}
{True:M106 P0}{False:M107 P0}
```

stuartpittaway, 2022-03-18:
> https://marlinfw.org/docs/gcode/M042.html Set Pin State - M42 Ignore Pin State Mode

Probably don't need those pin states as the outputs on the mobo are connected to the fan header/pins, so M106 can be used.

InfiniteNesLives, 2022-04-07:
Bumping this issue as people are still actively running into this problem..

sphawes, 2022-05-11:
@InfiniteNesLives Thanks for reporting this, definitely incorrect on the docs side; should have the extra line to actuate the valve as well. This will be fixed with the next documentation release we're prepping for now!

Closed 2022-05-17.

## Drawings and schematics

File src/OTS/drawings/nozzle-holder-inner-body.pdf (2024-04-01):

19.25

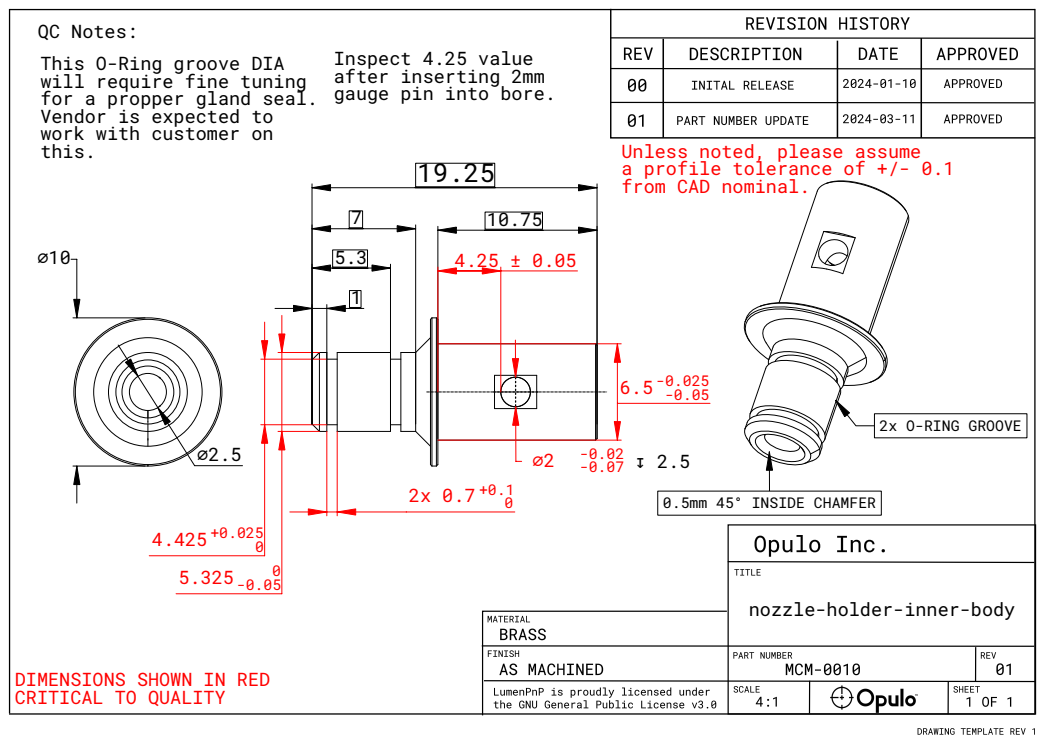
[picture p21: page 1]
0.5mm 45° INSIDE CHAMFER; 2x O-RING GROOVE

QC Notes:
This O-Ring groove DIA
will require fine tuning for a propper gland seal.
Vendor is expected to
work with customer on
this.

Inspect 4.25 value
after inserting 2mm
gauge pin into bore.

Unless noted, please assume
a profile tolerance of +/- 0.1
from CAD nominal.

nozzle-holder-inner-body

DIMENSIONS SHOWN IN RED
CRITICAL TO QUALITY

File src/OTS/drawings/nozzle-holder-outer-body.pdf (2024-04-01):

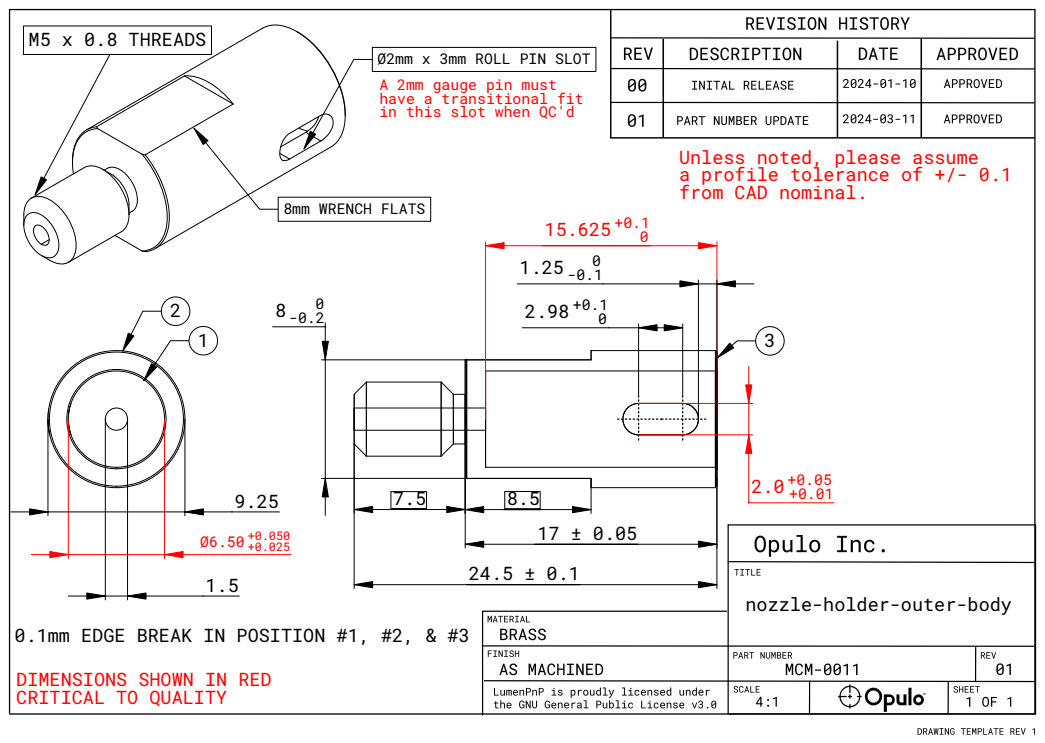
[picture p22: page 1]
8mm WRENCH FLATS; M5 x 0.8 THREADS

Ø2mm x 3mm ROLL PIN SLOT
A 2mm gauge pin must
have a transitional fit
in this slot when QC'd

Unless noted, please assume
a profile tolerance of +/- 0.1
from CAD nominal.

nozzle-holder-outer-body

0.1mm EDGE BREAK IN POSITION #1, #2, & #3

DIMENSIONS SHOWN IN RED
CRITICAL TO QUALITY

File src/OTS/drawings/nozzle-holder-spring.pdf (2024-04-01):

## Specification (Metric)

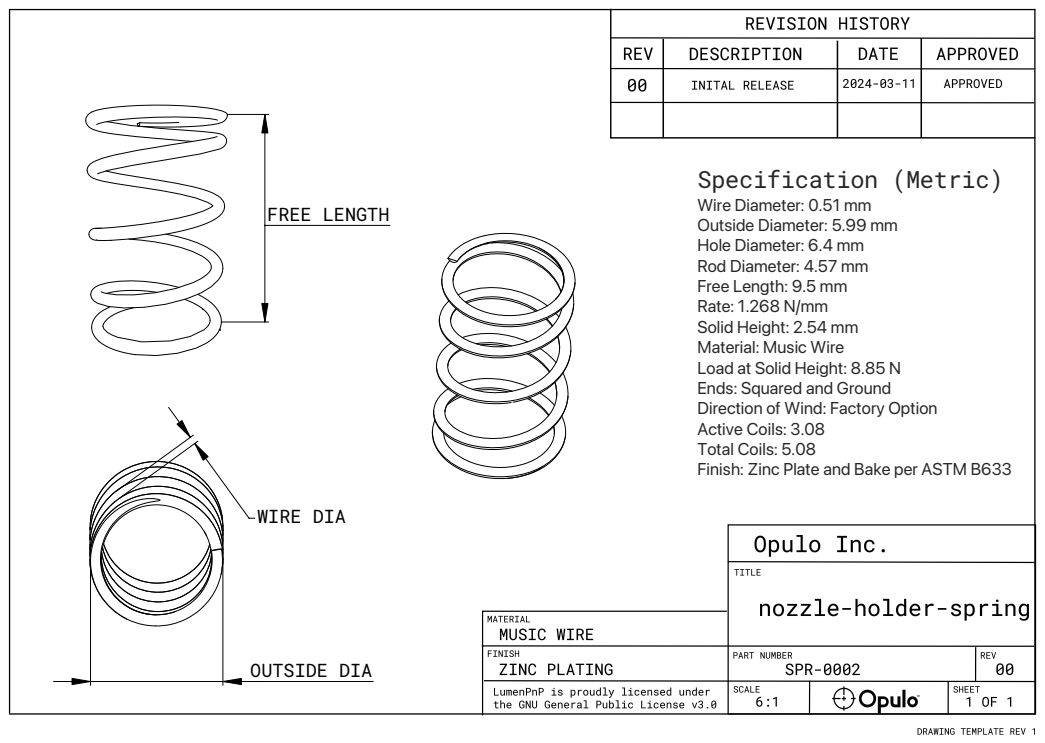
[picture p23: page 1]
FREE LENGTH; OUTSIDE DIA; WIRE DIA

Wire Diameter: 0.51 mm
Outside Diameter: 5.99 mm
Hole Diameter: 6.4 mm
Rod Diameter: 4.57 mm
Free Length: 9.5 mm
Rate: 1.268 N/mm
Solid Height: 2.54 mm
Material: Music Wire
Load at Solid Height: 8.85 N
Ends: Squared and Ground
Direction of Wind: Factory Option
Active Coils: 3.08
Total Coils: 5.08
Finish: Zinc Plate and Bake per ASTM B633

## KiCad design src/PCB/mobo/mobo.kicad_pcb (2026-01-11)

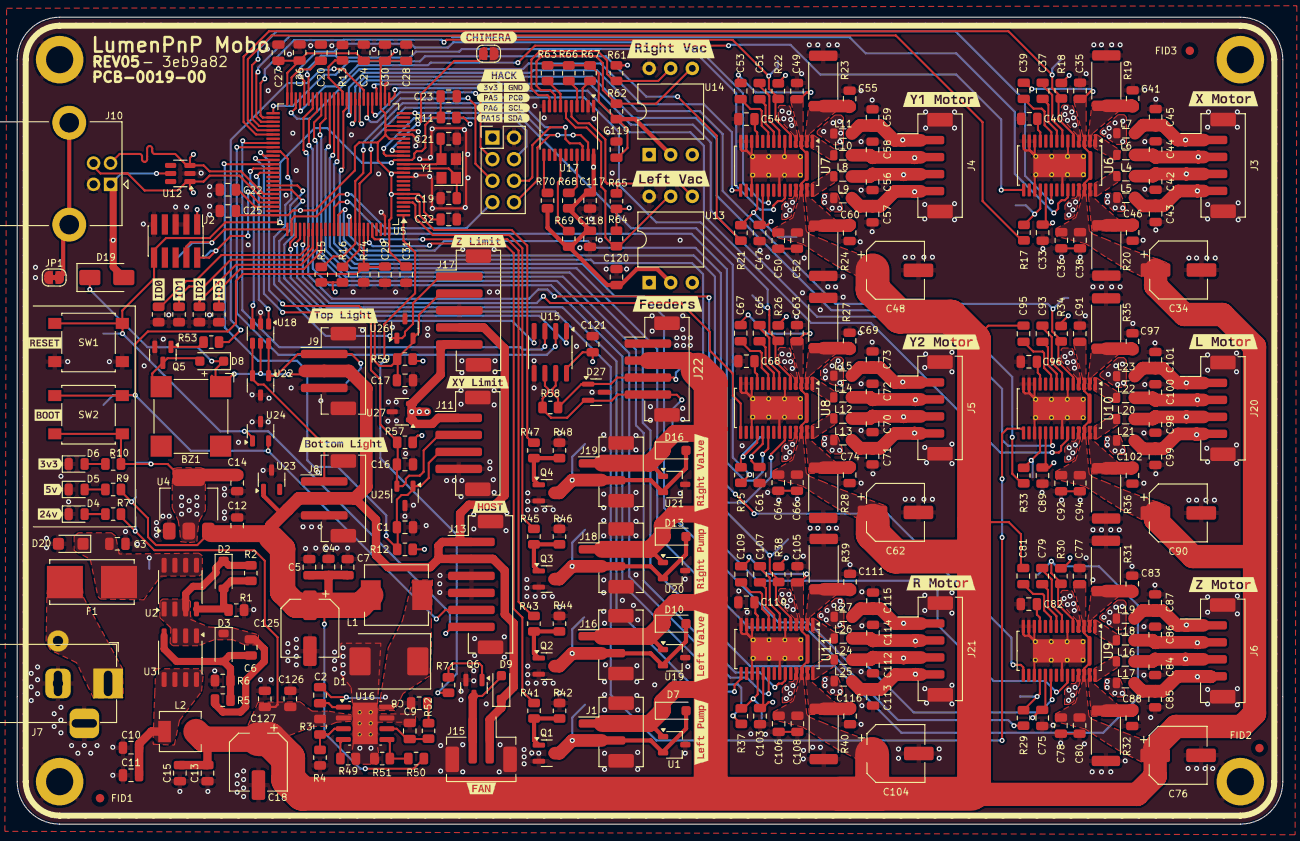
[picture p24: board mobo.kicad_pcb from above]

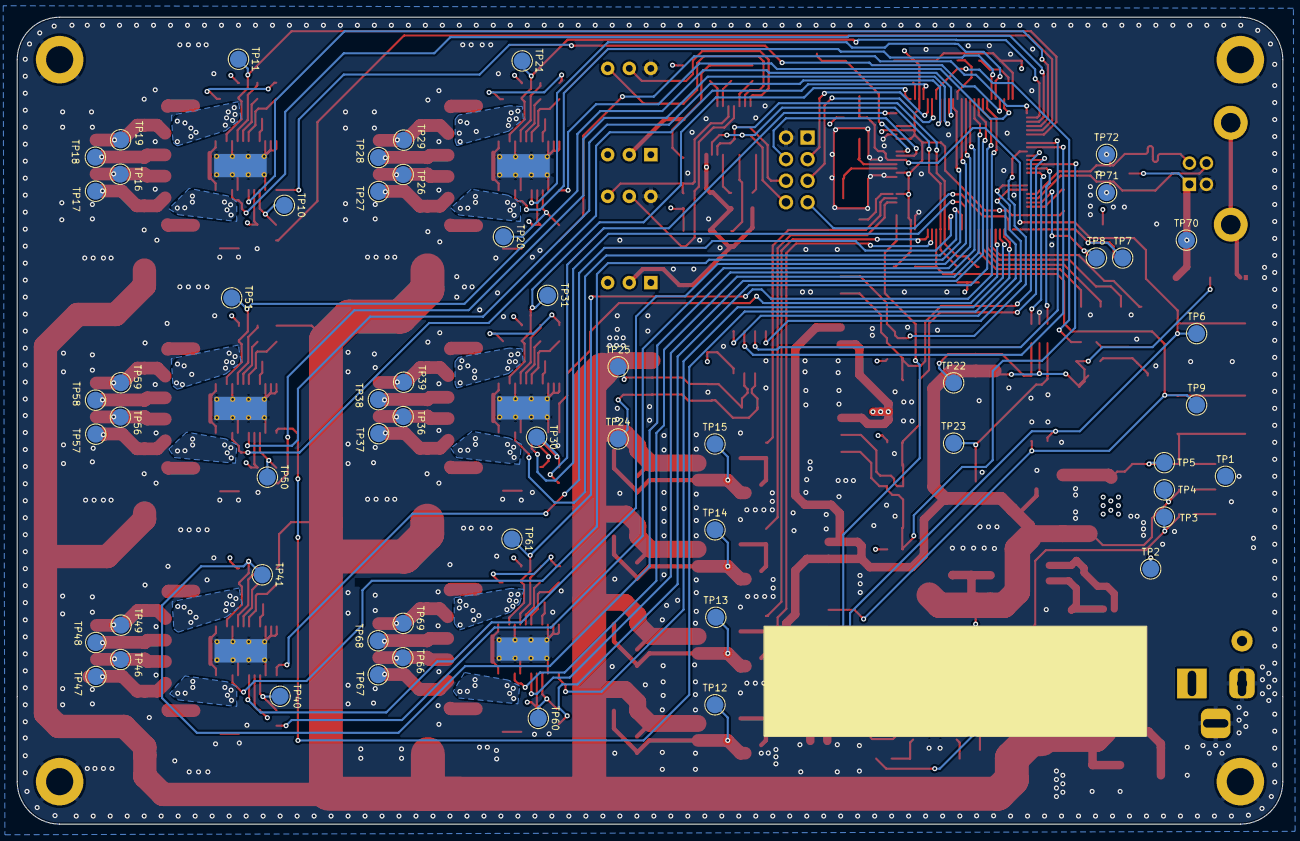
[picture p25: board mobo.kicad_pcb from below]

Board: 4 copper layers, 149.0 x 95.0 mm, 399 parts (57 on the bottom side), 206 nets.

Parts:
BZ1: Buzzer; MagneticBuzzer_CUI_CMT-8504-100-SMT
C1, C6, C16, C17, C23, C26, C27, C28, C29, C30, C31, C32, C33, C36, C38, C39, C41, C46, C47, C50, C52, C53, C55, C60, C61, C64, C66, C67, C69, C74, C75, C78, C80, C81, C83, C88, C89, C92, C94, C95, C97, C102, C103, C106, C108, C109, C111, C116, C117, C119, C120, C121: 100n; C_0805_2012Metric
C2: 0.1u; C_0805_2012Metric
C3, C4, C5, C7, C10, C11, C12, C13, C14, C15, C35, C49, C63, C77, C91, C105, C118, C126, C127: 10u; C_0805_2012Metric
C8: 4.7n; C_0805_2012Metric
C9: 47p; C_0805_2012Metric
C18, C34, C48, C62, C76, C90, C104, C125: 100u; CP_Elec_6.3x7.7
C19, C21: 10p; C_0805_2012Metric
C20, C22, C24, C25: 2u2; C_0805_2012Metric
C37, C51, C65, C79, C93, C107: 22n; C_0805_2012Metric
C40, C54, C68, C82, C96, C110: 4.7u; C_0805_2012Metric
C42, C43, C44, C45, C56, C57, C58, C59, C70, C71, C72, C73, C84, C85, C86, C87, C98, C99, C100, C101, C112, C113, C114, C115: 470p; C_0805_2012Metric
D1: B560C; D_SMC
D2, D3: BZT52C16; D_SOD-123
D4, D5, D6: Yellow; LED_0805_2012Metric
D7, D8, D9, D10, D13, D16: SM4007; D_SOD-123F
D19: SS34; D_SMA
D20: SMF28A; D_SMF
D27: SM712_SOT23; SOT-23
F1: Fuse; Fuseholder_Littelfuse_Nano2_154x
FID1, FID2, FID3: Fiducial; Fiducial_1mm_Mask2mm
G1: Opulo-Logo; logo_mask
G2: Goblin-logo; goblin
H1, H2, H3, H4: MountingHole_Pad; MountingHole_3.2mm_M3_DIN965_Pad
J1, J16, J18, J19: FET; JST_PH_B2B-PH-SM4-TB_1x02-1MP_P2.00mm_Vertical
J2: SWD Header; PinHeader_2x05_P1.27mm_Vertical_SMD
J3, J4, J5, J6, J20, J21: MOTOR; JST_PH_B4B-PH-SM4-TB_1x04-1MP_P2.00mm_Vertical
J7: COMBO_POWER_JACK; BarrelJack_Horizontal
J8: BTM_LIGHT; JST_PH_B3B-PH-SM4-TB_1x03-1MP_P2.00mm_Vertical
J9: TOP_LIGHT; JST_PH_B3B-PH-SM4-TB_1x03-1MP_P2.00mm_Vertical
J10: USB_B; USB_B_Lumberg_2411_02_Horizontal
J11: XY_LIMIT; JST_PH_B4B-PH-SM4-TB_1x04-1MP_P2.00mm_Vertical
J13: HOST; JST_PH_B6B-PH-SM4-TB_1x06-1MP_P2.00mm_Vertical
J14: HACK_HEADER; PinHeader_2x04_P2.54mm_Vertical
J15: FAN; JST_PH_B2B-PH-SM4-TB_1x02-1MP_P2.00mm_Vertical
J17: Z_LIMIT; JST_PH_B5B-PH-SM4-TB_1x05-1MP_P2.00mm_Vertical
J22: FEEDERS; JST_PH_B4B-PH-SM4-TB_1x04-1MP_P2.00mm_Vertical
JP1: SHIELD_GND; SolderJumper-2_P1.3mm_Bridged_RoundedPad1.0x1.5mm
JP2: CHIMERA_JUMPER; SolderJumper-2_P1.3mm_Open_RoundedPad1.0x1.5mm
L1: 7.2u; L_Sunlord_MWSA0603S
L2: 2.2u; L_Sunlord_MWSA0402S
L4, L5, L6, L7, L8, L9, L10, L11, L12, L13, L14, L15, L16, L17, L18, L19, L20, L21, L22, L23, L24, L25, L26, L27: L_Ferrite; L_0805_2012Metric
Q1, Q2, Q3, Q4, Q5, Q6: AO3400A; SOT-23
R1, R3, R6, R7, R11, R13, R14, R18, R22, R26, R30, R34, R38, R42, R44, R46, R48, R51, R63, R66, R67, R68, R69, R70: 10k; R_0805_2012Metric
R2, R5, R15, R16: 4.7k; R_0805_2012Metric
R4, R9: 2.7k; R_0805_2012Metric
R8, R54, R55, R56: 0R; R_0805_2012Metric
R10, R17, R21, R25, R29, R33, R37: 1k; R_0805_2012Metric
R12, R57, R59: 10K; R_0805_2012Metric
R19, R20, R23, R24, R27, R28, R31, R32, R35, R36, R39, R40: 120m; R_2512_6332Metric
R41, R43, R45, R47, R58: 120; R_0805_2012Metric
R49: 243k; R_0805_2012Metric
R50: 53.6k; R_0805_2012Metric
R52: 16.9k; R_0805_2012Metric
R53, R71: 120R; R_0805_2012Metric
R61, R62, R64, R65: 4k7; R_0805_2012Metric
SW1, SW2: SW_Push; SW_SPST_B3S-1000
TP1, TP2, TP3, TP4, TP5, TP6, TP7, TP8, TP9, TP10, TP11, TP12, TP13, TP14, TP15, TP16, TP17, TP18, TP19, TP20, TP21, TP22, TP23, TP24, TP25, TP26, TP27, TP28, TP29, TP30, TP31, TP36, TP37, TP38, TP39, TP40, TP41, TP46, TP47, TP48, TP49, TP50, TP51, TP56, TP57, TP58, TP59, TP60, TP61, TP66, TP67, TP68, TP69, TP70, TP71, TP72: TestPoint; TestPoint_Pad_D2.0mm
U1, U19, U20, U21: TSOT-23
U2, U3: FDS4435BZ; SO-8_3.9x4.9mm_P1.27mm
U4: AP1117-33; SOT-223-3_TabPin2
U5: STM32F407VETx; LQFP-100_14x14mm_P0.5mm
U6, U7, U8, U9, U10, U11: TMC2226-SA; HTSSOP-28-1EP_4.4x9.7mm_P0.65mm_EP2.75x6.2mm_ThermalVias
U12: SRV05-4; SOT-23-6
U13, U14: XGZP6857D; DIP-6_W10.16mm
U15: MAX3078E; SOIC-8_3.9x4.9mm_P1.27mm
U16: TPS54560BDDA; Texas_R-PDSO-G8_EP2.95x4.9mm_Mask2.4x3.1mm_ThermalVias
U17: PCA9545A; TSSOP-20_4.4x6.5mm_P0.65mm
U18: SN74LVC2G34; SOT-23-6
U22, U23: PESD5V2S2UT; SOT-23-3
U24, U25, U26, U27: PESD3V3S2UT; SOT-23-3
Y1: 8MHz; Crystal_SMD_3225-4Pin_3.2x2.5mm
kibuzzard-65DCF286: G***; kibuzzard-65DCF286
kibuzzard-65E24FAE: G***; kibuzzard-65E24FAE
kibuzzard-65E215D8: G***; kibuzzard-65E215D8
kibuzzard-65E215EC: G***; kibuzzard-65E215EC
kibuzzard-65E240B2: G***; kibuzzard-65E240B2
kibuzzard-65E241C9: G***; kibuzzard-65E241C9
kibuzzard-65E2151D: G***; kibuzzard-65E2151D
kibuzzard-65E2155B: G***; kibuzzard-65E2155B
kibuzzard-65E2156F: G***; kibuzzard-65E2156F
kibuzzard-65E2408C: G***; kibuzzard-65E2408C
kibuzzard-65E2409D: G***; kibuzzard-65E2409D
kibuzzard-65E2504F: G***; kibuzzard-65E2504F
kibuzzard-65E24108: G***; kibuzzard-65E24108
kibuzzard-65E24112: G***; kibuzzard-65E24112
kibuzzard-65E24141: G***; kibuzzard-65E24141
kibuzzard-65E25035: G***; kibuzzard-65E25035
kibuzzard-65E25071: G***; kibuzzard-65E25071
kibuzzard-65F1FEA3: G***; kibuzzard-65F1FEA3
kibuzzard-6585C0AF: G***; kibuzzard-6585C0AF
kibuzzard-6585C0D3: G***; kibuzzard-6585C0D3
kibuzzard-6585C08F: G***; kibuzzard-6585C08F
kibuzzard-6585C058: G***; kibuzzard-6585C058
kibuzzard-6606EA2E: G***; kibuzzard-6606EA2E
kibuzzard-6606EA4F: G***; kibuzzard-6606EA4F
kibuzzard-6606EA6E: G***; kibuzzard-6606EA6E
kibuzzard-65709CC6: G***; kibuzzard-65709CC6
kibuzzard-65709E62: G***; kibuzzard-65709E62
kibuzzard-65848E86: G***; kibuzzard-65848E86
kibuzzard-65848E91: G***; kibuzzard-65848E91
kibuzzard-65848EB6: G***; kibuzzard-65848EB6
kibuzzard-65848FCC: G***; kibuzzard-65848FCC
kibuzzard-65848FD5: G***; kibuzzard-65848FD5
kibuzzard-65848FDC: G***; kibuzzard-65848FDC
kibuzzard-65848FE3: G***; kibuzzard-65848FE3
kibuzzard-65848FE9: G***; kibuzzard-65848FE9
kibuzzard-65848FEF: G***; kibuzzard-65848FEF
kibuzzard-660711AC: G***; kibuzzard-660711AC
kibuzzard-66071149: G***; kibuzzard-66071149

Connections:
+3.3V: C14.1, C24.1, C25.1, C26.1, C27.1, C28.1, C30.1, C31.1, C32.1, C33.2, C47.2, C61.2, C75.2, C89.2, C103.2, C117.1, C118.1, C119.1, C120.1, C121.2, J2.1 (VTref), J11.1, J14.1, J17.5, R10.1, R11.1, R12.2, R15.1, R16.1, R18.1, R22.1, R26.1, R30.1, R34.1, R38.1, R57.2, R59.2, R61.2, R62.2, R63.1, R64.1, R65.1, R66.1, R67.1, R68.2, R69.2, R70.2, SW2.2, TP5.1, U4.2 (VO), U5.6 (VBAT), U5.11 (VDD), U5.19 (VDD), U5.21 (VREF+), U5.22 (VDDA), U5.28 (VDD), U5.50 (VDD), U5.75 (VDD), U5.100 (VDD), U6.19 (VCC_IO), U7.19 (VCC_IO), U8.19 (VCC_IO), U9.19 (VCC_IO), U10.19 (VCC_IO), U11.19 (VCC_IO), U13.2 (VDD), U14.2 (VDD), U15.8 (VCC), U17.20 (VDD), U27.1, U27.2
+5V: BZ1.1 (-), C4.2, C5.2, C7.2, C12.1, C125.1, D8.1 (K), D9.1 (K), D19.1 (K), J8.2, J9.2, J13.1, J13.2, J15.1, J17.4, L1.2, R9.1, R50.1, TP4.1, U4.3 (VI), U18.5 (VCC), U23.1
/Lighting/BTM_LIGHT: U5.64 (PC7), U18.3 (2A)
/Microcontroller/AUX: J17.1, U5.60 (PD13), U26.1
/Microcontroller/BOOT1: R13.1, U5.37 (PB2)
/Microcontroller/BUZZER: R53.1, U5.32 (PA7)
/Microcontroller/CHIMERA: JP2.1 (A), U5.16 (PC1)
/Microcontroller/FAN: R71.1, U5.1 (PE2)
/Microcontroller/I2C_SCL: J14.6, R15.2, U5.92 (PB6), U17.18 (SCL)
/Microcontroller/I2C_SDA: J14.8, R16.2, U5.93 (PB7), U17.19 (SDA)
/Microcontroller/ID0: R8.2, U5.81 (PD0)
/Microcontroller/ID1: R54.2, U5.82 (PD1)
/Microcontroller/ID2: R55.2, U5.83 (PD2)
/Microcontroller/ID3: R56.2, U5.84 (PD3)
/Microcontroller/LUMEN_AUX_A1: J14.4, U5.15 (PC0)
/Microcontroller/LUMEN_AUX_PWM1: J14.3, U5.30 (PA5)
/Microcontroller/LUMEN_AUX_PWM2: J14.5, U5.31 (PA6)
/Microcontroller/LUMEN_AUX_PWM3: J14.7, U5.77 (PA15)
/Microcontroller/MOS1: R41.2, U5.95 (PB8)
/Microcontroller/MOS2: R43.2, U5.96 (PB9)
/Microcontroller/MOS3: R45.2, U5.4 (PE5)
/Microcontroller/MOS4: R47.2, U5.5 (PE6)
/Microcontroller/PA2: R25.2, U5.25 (PA2)
/Microcontroller/PA3: R26.2, TP31.1, U5.26 (PA3), U8.5 (~EN)
/Microcontroller/PA4: U5.29 (PA4), U10.23 (DIR)
/Microcontroller/PB0: R34.2, TP51.1, U5.35 (PB0), U10.5 (~EN)
/Microcontroller/PB1: U5.36 (PB1), U9.23 (DIR)
/Microcontroller/PB5: U5.91 (PB5), U9.15 (DIAG)
/Microcontroller/PB10: U5.47 (PB10), U6.15 (DIAG)
/Microcontroller/PB11: U5.48 (PB11), U7.15 (DIAG)
/Microcontroller/PB12: R21.2, U5.51 (PB12)
/Microcontroller/PB13: R22.2, TP21.1, U5.52 (PB13), U7.5 (~EN)
/Microcontroller/PB14: U5.53 (PB14), U6.23 (DIR)
/Microcontroller/PB15: U5.54 (PB15), U6.20 (STEP)
/Microcontroller/PC4: U5.33 (PC4), U10.20 (STEP)
/Microcontroller/PC5: R33.2, U5.34 (PC5)
/Microcontroller/PC10: U5.78 (PC10), U10.15 (DIAG)
/Microcontroller/PC11: U5.79 (PC11), U11.15 (DIAG)
/Microcontroller/PC12: U5.80 (PC12), U8.15 (DIAG)
/Microcontroller/PD6: U5.87 (PD6), U8.20 (STEP)
/Microcontroller/PD7: U5.88 (PD7), U8.23 (DIR)
/Microcontroller/PD9: R18.2, TP11.1, U5.56 (PD9), U6.5 (~EN)
/Microcontroller/PE7: U5.38 (PE7), U9.20 (STEP)
/Microcontroller/PE8: R29.2, U5.39 (PE8)
/Microcontroller/PE9: R30.2, TP41.1, U5.40 (PE9), U9.5 (~EN)
/Microcontroller/PE10: U5.41 (PE10), U11.23 (DIR)
/Microcontroller/PE11: U5.42 (PE11), U11.20 (STEP)
/Microcontroller/PE12: R37.2, U5.43 (PE12)
/Microcontroller/PE13: R38.2, TP61.1, U5.44 (PE13), U11.5 (~EN)
/Microcontroller/PE14: U5.45 (PE14), U7.23 (DIR)
/Microcontroller/PE15: U5.46 (PE15), U7.20 (STEP)
/Microcontroller/RS485_DE: U5.58 (PD11), U15.3 (DE)
/Microcontroller/RS485_RE: U5.59 (PD12), U15.2 (~RE)
/Microcontroller/RS485_RX: U5.69 (PA10), U15.1 (RO)
/Microcontroller/RS485_TX: U5.68 (PA9), U15.4 (DI)
/Microcontroller/SWCLK: J2.4 (SWDCLK/TCK), TP7.1, U5.76 (PA14)
/Microcontroller/SWDIO: J2.2 (SWDIO/TMS), TP8.1, U5.72 (PA13)
/Microcontroller/USB_D+: J10.3 (D+), TP71.1, U5.71 (PA12), U12.1 (IO1)
/Microcontroller/USB_D-: J10.2 (D-), TP72.1, U5.70 (PA11), U12.3 (IO2)
/Microcontroller/X_LIMIT: C1.1, J11.3, R12.1, U5.63 (PC6), U25.1
/Microcontroller/X_UART: R17.2, U5.55 (PD8)
/Microcontroller/Y_LIMIT: C16.1, J11.2, R57.1, U5.62 (PD15), U25.2
/Microcontroller/Z_LIMIT: C17.1, J17.2, R59.1, U5.61 (PD14), U26.2
/Motor L/5VOUT: C96.2, U10.11 (5VOUT)
/Motor L/A1: C98.2, J20.3, L20.2, TP56.1
/Motor L/A2: C99.1, J20.4, L21.2, TP57.1
/Motor L/B1: C100.2, J20.2, L22.2, TP58.1
/Motor L/B2: C101.1, J20.1, L23.2, TP59.1
/Motor R/5VOUT: C110.2, U11.11 (5VOUT)
/Motor R/A1: C112.2, J21.3, L24.2, TP66.1
/Motor R/A2: C113.1, J21.4, L25.2, TP67.1
/Motor R/B1: C114.2, J21.2, L26.2, TP68.1
/Motor R/B2: C115.1, J21.1, L27.2, TP69.1
/Motor X/5VOUT: C40.2, U6.11 (5VOUT)
/Motor X/A1: C42.2, J3.3, L4.2, TP16.1
/Motor X/A2: C43.1, J3.4, L5.2, TP17.1
/Motor X/B1: C44.2, J3.2, L6.2, TP18.1
/Motor X/B2: C45.1, J3.1, L7.2, TP19.1
/Motor Y1/5VOUT: C54.2, U7.11 (5VOUT)
/Motor Y1/A1: C56.2, J4.3, L8.2, TP26.1
/Motor Y1/A2: C57.1, J4.4, L9.2, TP27.1
/Motor Y1/B1: C58.2, J4.2, L10.2, TP28.1
/Motor Y1/B2: C59.1, J4.1, L11.2, TP29.1
/Motor Y2/5VOUT: C68.2, U8.11 (5VOUT)
/Motor Y2/A1: C70.2, J5.3, L12.2, TP36.1
/Motor Y2/A2: C71.1, J5.4, L13.2, TP37.1
/Motor Y2/B1: C72.2, J5.2, L14.2, TP38.1
/Motor Y2/B2: C73.1, J5.1, L15.2, TP39.1
/Motor Z/5VOUT: C82.2, U9.11 (5VOUT)
/Motor Z/A1: C84.2, J6.3, L16.2, TP46.1
/Motor Z/A2: C85.1, J6.4, L17.2, TP47.1
/Motor Z/B1: C86.2, J6.2, L18.2, TP48.1
/Motor Z/B2: C87.1, J6.1, L19.2, TP49.1
/Power/POWER_SUPPLY: F1.1, J7.1, J7.4
/Power/VIN: C3.2, D20.1 (A1), F1.2, TP2.1, U2.5 (D), U2.6 (D), U2.7 (D), U2.8 (D)
/RS485/RS-485+: D27.2 (A2), J22.4, R58.1, TP24.1, U15.6 (A)
/RS485/RS-485-: D27.1 (A1), J22.3, R58.2, TP25.1, U15.7 (B)
/Vacuum sensors/SC0: R64.2, U13.5 (SCL), U17.6 (SC0)
/Vacuum sensors/SC1: R61.1, U14.5 (SCL), U17.9 (SC1)
/Vacuum sensors/SD0: R65.2, U13.4 (SDA), U17.5 (SD0)
/Vacuum sensors/SD1: R62.1, U14.4 (SDA), U17.8 (SD1)
BOOT: C29.1, J13.5, R14.1, SW2.1, TP9.1, U5.94 (BOOT0), U24.2
GND: C1.2, C3.1, C4.1, C5.1, C7.1, C8.1, C9.1, C10.1, C11.1, C12.2, C13.1, C14.2, C15.1, C16.2, C17.2, C18.2, C19.2, C20.2, C21.2, C22.2, C23.2, C24.2, C25.2, C26.2, C27.2, C28.2, C29.2, C30.2, C31.2, C32.2, C33.1, C34.2, C35.1, C36.1, C38.1, C40.1, C41.1, C42.1, C43.2, C44.1, C45.2, C46.1, C47.1, C48.2, C49.1, C50.1, C52.1, C54.1, C55.1, C56.1, C57.2, C58.1, C59.2, C60.1, C61.1, C62.2, C63.1, C64.1, C66.1, C68.1, C69.1, C70.1, C71.2, C72.1, C73.2, C74.1, C75.1, C76.2, C77.1, C78.1, C80.1, C82.1, C83.1, C84.1, C85.2, C86.1, C87.2, C88.1, C89.1, C90.2, C91.1, C92.1, C94.1, C96.1, C97.1, C98.1, C99.2, C100.1, C101.2, C102.1, C103.1, C104.2, C105.1, C106.1, C108.1, C110.1, C111.1, C112.1, C113.2, C114.1, C115.2, C116.1, C117.2, C118.2, C119.2, C120.2, C121.1, C125.2, C126.1, C127.1, D1.2 (A), D4.1 (K), D5.1 (K), D6.1 (K), D20.2 (A2), D27.3 (common), H1.1, H2.1, H3.1, H4.1, J1.MP (MountPin), J2.3 (GND), J2.5 (GND), J2.9 (GNDDetect), J3.MP (MountPin), J4.MP (MountPin), J5.MP (MountPin), J6.MP (MountPin), J7.2, J7.3, J8.3, J8.MP (MountPin), J9.3, J9.MP (MountPin), J10.4 (GND), J11.4, J11.MP (MountPin), J13.3, J13.4, J13.MP (MountPin), J14.2, J15.MP (MountPin), J16.MP (MountPin), J17.3, J17.MP (MountPin), J18.MP (MountPin), J19.MP (MountPin), J20.MP (MountPin), J21.MP (MountPin), J22.1, J22.MP (MountPin), JP1.2 (B), JP2.2 (B), Q1.2 (S), Q2.2 (S), Q3.2 (S), Q4.2 (S), Q5.2 (S), Q6.2 (S), R1.2, R4.2, R6.2, R8.1, R13.2, R14.2, R19.2, R20.2, R23.2, R24.2, R27.2, R28.2, R31.2, R32.2, R35.2, R36.2, R39.2, R40.2, R42.1, R44.1, R46.1, R48.1, R49.2, R51.2, R54.1, R55.1, R56.1, SW1.1, TP1.1, U1.3, U4.1 (GND), U5.10 (VSS), U5.20 (VSSA), U5.27 (VSS), U5.74 (VSS), U5.99 (VSS), U6.6 (GND), U6.12 (MS1_AD0), U6.13 (NC), U6.14 (MS2_AD1), U6.17 (CLK), U6.22 (GND), U6.29 (GND), U7.6 (GND), U7.12 (MS1_AD0), U7.13 (NC), U7.14 (MS2_AD1), U7.17 (CLK), U7.22 (GND), U7.29 (GND), U8.6 (GND), U8.12 (MS1_AD0), U8.13 (NC), U8.14 (MS2_AD1), U8.17 (CLK), U8.22 (GND), U8.29 (GND), U9.6 (GND), U9.12 (MS1_AD0), U9.13 (NC), U9.14 (MS2_AD1), U9.17 (CLK), U9.22 (GND), U9.29 (GND), U10.6 (GND), U10.12 (MS1_AD0), U10.13 (NC), U10.14 (MS2_AD1), U10.17 (CLK), U10.22 (GND), U10.29 (GND), U11.6 (GND), U11.12 (MS1_AD0), U11.13 (NC), U11.14 (MS2_AD1), U11.17 (CLK), U11.22 (GND), U11.29 (GND), U12.2 (VN), U13.6 (GND), U14.6 (GND), U15.5 (GND), U16.7 (GND), U16.9 (GND), U17.1 (A0), U17.2 (A1), U17.10 (VSS), U18.2 (GND), U19.3, U20.3, U21.3, U22.3, U23.3, U24.3, U25.3, U26.3, U27.3, Y1.2, Y1.4
unnamed: BZ1.2 (+), D8.2 (A), Q5.3 (D)
unnamed: C8.2, R52.2
unnamed: C10.2, C11.2, L2.1, U3.5 (D), U3.6 (D), U3.7 (D), U3.8 (D)
unnamed: C2.1, D1.1 (K), L1.1, U16.8 (SW)
unnamed: D2.2 (A), R1.1, R2.2, U2.4 (G)
unnamed: C6.2, D2.1 (K), D3.1 (K), R2.1, R5.1, U2.1 (S), U2.2 (S), U2.3 (S), U3.1 (S), U3.2 (S), U3.3 (S)
unnamed: C6.1, D3.2 (A), R5.2, R6.1, U3.4 (G)
unnamed: D4.2 (A), R7.2
unnamed: D5.2 (A), R9.2
unnamed: D6.2 (A), R10.2
unnamed: D7.2 (A), J1.2, Q1.3 (D), TP12.1, U1.2
unnamed: D9.2 (A), J15.2, Q6.3 (D)
unnamed: D10.2 (A), J16.2, Q2.3 (D), TP13.1, U19.2
unnamed: D13.2 (A), J18.2, Q3.3 (D), TP14.1, U20.2
unnamed: D16.2 (A), J19.2, Q4.3 (D), TP15.1, U21.2
unnamed: J8.1, TP23.1, U18.4 (2Y), U22.2
unnamed: J9.1, TP22.1, U18.6 (1Y), U22.1
unnamed: J10.5 (Shield), JP1.1 (A)
unnamed: Q1.1 (G), R41.1, R42.2
unnamed: Q2.1 (G), R43.1, R44.2
unnamed: Q3.1 (G), R45.1, R46.2
unnamed: Q4.1 (G), R47.1, R48.2
unnamed: Q5.1 (G), R53.2
unnamed: Q6.1 (G), R71.2
unnamed: C19.1, U5.12 (PH0), Y1.1
unnamed: C21.1, U5.13 (PH1), Y1.3
unnamed: C20.1, U5.49 (VCAP_1)
unnamed: C22.1, U5.73 (VCAP_2)
unnamed: C46.2, R20.1, U6.27 (BRA)
unnamed: C41.2, R19.1, U6.2 (BRB)
unnamed: C37.2, U6.8 (CPI)
unnamed: C37.1, U6.7 (CPO)
unnamed: L4.1, U6.28 (OA1)
unnamed: L5.1, U6.25 (OA2)
unnamed: L6.1, U6.1 (OB1)
unnamed: L7.1, U6.4 (OB2)
unnamed: R17.1, TP10.1, U6.18 (PDN_UART)
unnamed: C39.1, U6.9 (VCP)
unnamed: C60.2, R24.1, U7.27 (BRA)
unnamed: C55.2, R23.1, U7.2 (BRB)
unnamed: C51.2, U7.8 (CPI)
unnamed: C51.1, U7.7 (CPO)
unnamed: L8.1, U7.28 (OA1)
unnamed: L9.1, U7.25 (OA2)
unnamed: L10.1, U7.1 (OB1)
unnamed: L11.1, U7.4 (OB2)
unnamed: R21.1, TP20.1, U7.18 (PDN_UART)
unnamed: C53.1, U7.9 (VCP)
unnamed: C74.2, R28.1, U8.27 (BRA)
unnamed: C69.2, R27.1, U8.2 (BRB)
unnamed: C65.2, U8.8 (CPI)
unnamed: C65.1, U8.7 (CPO)
unnamed: L12.1, U8.28 (OA1)
unnamed: L13.1, U8.25 (OA2)
unnamed: L14.1, U8.1 (OB1)
unnamed: L15.1, U8.4 (OB2)
unnamed: R25.1, TP30.1, U8.18 (PDN_UART)
unnamed: C67.1, U8.9 (VCP)
unnamed: C88.2, R32.1, U9.27 (BRA)
unnamed: C83.2, R31.1, U9.2 (BRB)
unnamed: C79.2, U9.8 (CPI)
unnamed: C79.1, U9.7 (CPO)
unnamed: L16.1, U9.28 (OA1)
unnamed: L17.1, U9.25 (OA2)
unnamed: L18.1, U9.1 (OB1)
unnamed: L19.1, U9.4 (OB2)
unnamed: R29.1, TP40.1, U9.18 (PDN_UART)
unnamed: C81.1, U9.9 (VCP)
unnamed: C102.2, R36.1, U10.27 (BRA)
unnamed: C97.2, R35.1, U10.2 (BRB)
unnamed: C93.2, U10.8 (CPI)
unnamed: C93.1, U10.7 (CPO)
unnamed: L20.1, U10.28 (OA1)
unnamed: L21.1, U10.25 (OA2)
unnamed: L22.1, U10.1 (OB1)
unnamed: L23.1, U10.4 (OB2)
unnamed: R33.1, TP50.1, U10.18 (PDN_UART)
unnamed: C95.1, U10.9 (VCP)
unnamed: C116.2, R40.1, U11.27 (BRA)
unnamed: C111.2, R39.1, U11.2 (BRB)
unnamed: C107.2, U11.8 (CPI)
unnamed: C107.1, U11.7 (CPO)
unnamed: L24.1, U11.28 (OA1)
unnamed: L25.1, U11.25 (OA2)
unnamed: L26.1, U11.1 (OB1)
unnamed: L27.1, U11.4 (OB2)
unnamed: R37.1, TP60.1, U11.18 (PDN_UART)
unnamed: C109.1, U11.9 (VCP)
unnamed: C2.2, U16.1 (BOOT)
unnamed: C9.2, R52.1, U16.6 (COMP)
unnamed: R3.2, R4.1, U16.3 (EN)
unnamed: R50.2, R51.1, U16.5 (FB)
unnamed: R49.1, U16.4 (RT/CLK)
unnamed: R66.2, U17.4 (_INT0_)
unnamed: R63.2, U17.7 (_INT1_)
unnamed: R70.1, U17.11 (_INT2_)
unnamed: R69.1, U17.14 (_INT3_)
unnamed: R68.1, U17.17 (_INT_)
unnamed: R67.2, U17.3 (_RESET_)
RESET: C23.1, J2.10 (~RESET), J13.6, R11.2, SW1.2, TP6.1, U5.14 (NRST), U24.1
TOP_LIGHT: U5.65 (PC8), U18.1 (1A)
VBUS: D19.2 (A), J10.1 (VBUS), TP70.1, U12.5 (VP)
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

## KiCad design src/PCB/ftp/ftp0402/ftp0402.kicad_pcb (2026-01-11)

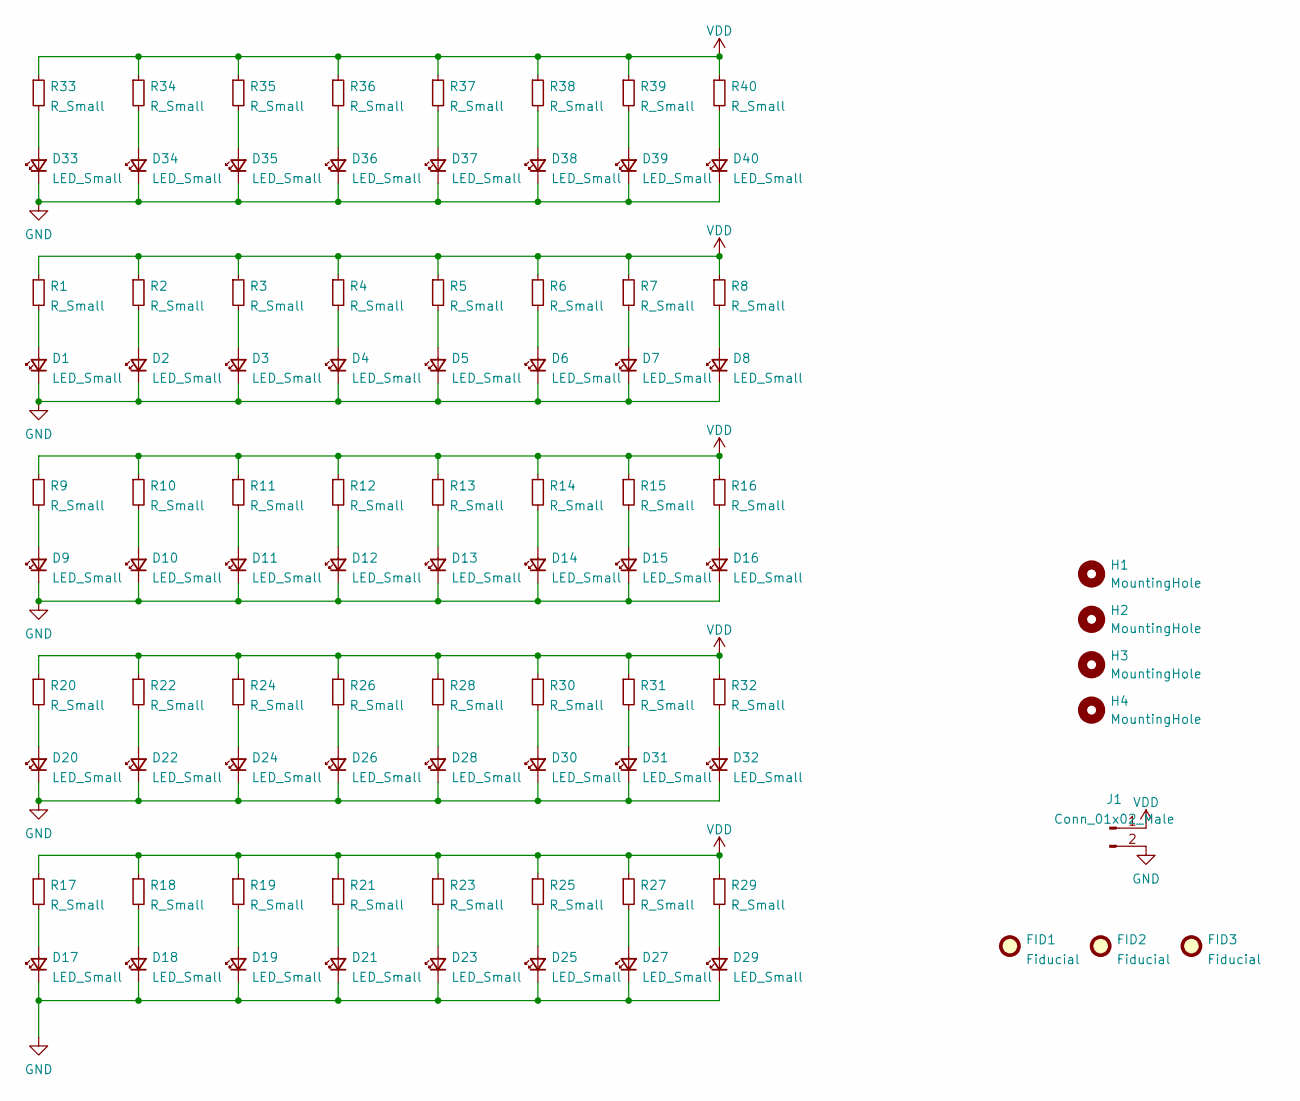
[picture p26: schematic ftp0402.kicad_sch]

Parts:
D1, D2, D3, D4, D5, D6, D7, D8, D9, D10, D11, D12, D13, D14, D15, D16, D17, D18, D19, D20, D21, D22, D23, D24, D25, D26, D27, D28, D29, D30, D31, D32, D33, D34, D35, D36, D37, D38, D39, D40: LED_Small; LED_0402_1005Metric
FID1, FID2, FID3: Fiducial; Fiducial_1mm_Mask3mm
H1, H2, H3, H4: MountingHole; MountingHole_3.2mm_M3_DIN965_Pad
J1: Conn_01x02_Male; PinHeader_1x02_P2.54mm_Vertical
R1, R2, R3, R4, R5, R6, R7, R8, R9, R10, R11, R12, R13, R14, R15, R16, R17, R18, R19, R20, R21, R22, R23, R24, R25, R26, R27, R28, R29, R30, R31, R32, R33, R34, R35, R36, R37, R38, R39, R40: R_Small; R_0402_1005Metric

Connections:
GND: D1.1 (K), D2.1 (K), D3.1 (K), D4.1 (K), D5.1 (K), D6.1 (K), D7.1 (K), D8.1 (K), D9.1 (K), D10.1 (K), D11.1 (K), D12.1 (K), D13.1 (K), D14.1 (K), D15.1 (K), D16.1 (K), D17.1 (K), D18.1 (K), D19.1 (K), D20.1 (K), D21.1 (K), D22.1 (K), D23.1 (K), D24.1 (K), D25.1 (K), D26.1 (K), D27.1 (K), D28.1 (K), D29.1 (K), D30.1 (K), D31.1 (K), D32.1 (K), D33.1 (K), D34.1 (K), D35.1 (K), D36.1 (K), D37.1 (K), D38.1 (K), D39.1 (K), D40.1 (K), J1.2
unnamed: D1.2 (A), R1.2
unnamed: D2.2 (A), R2.2
unnamed: D3.2 (A), R3.2
unnamed: D4.2 (A), R4.2
unnamed: D5.2 (A), R5.2
unnamed: D6.2 (A), R6.2
unnamed: D7.2 (A), R7.2
unnamed: D8.2 (A), R8.2
unnamed: D9.2 (A), R9.2
unnamed: D10.2 (A), R10.2
unnamed: D11.2 (A), R11.2
unnamed: D12.2 (A), R12.2
unnamed: D13.2 (A), R13.2
unnamed: D14.2 (A), R14.2
unnamed: D15.2 (A), R15.2
unnamed: D16.2 (A), R16.2
unnamed: D17.2 (A), R17.2
unnamed: D18.2 (A), R18.2
unnamed: D19.2 (A), R19.2
unnamed: D20.2 (A), R20.2
unnamed: D21.2 (A), R21.2
unnamed: D22.2 (A), R22.2
unnamed: D23.2 (A), R23.2
unnamed: D24.2 (A), R24.2
unnamed: D25.2 (A), R25.2
unnamed: D26.2 (A), R26.2
unnamed: D27.2 (A), R27.2
unnamed: D28.2 (A), R28.2
unnamed: D29.2 (A), R29.2
unnamed: D30.2 (A), R30.2
unnamed: D31.2 (A), R31.2
unnamed: D32.2 (A), R32.2
unnamed: D33.2 (A), R33.2
unnamed: D34.2 (A), R34.2
unnamed: D35.2 (A), R35.2
unnamed: D36.2 (A), R36.2
unnamed: D37.2 (A), R37.2
unnamed: D38.2 (A), R38.2
unnamed: D39.2 (A), R39.2
unnamed: D40.2 (A), R40.2
VDD: J1.1, R1.1, R2.1, R3.1, R4.1, R5.1, R6.1, R7.1, R8.1, R9.1, R10.1, R11.1, R12.1, R13.1, R14.1, R15.1, R16.1, R17.1, R18.1, R19.1, R20.1, R21.1, R22.1, R23.1, R24.1, R25.1, R26.1, R27.1, R28.1, R29.1, R30.1, R31.1, R32.1, R33.1, R34.1, R35.1, R36.1, R37.1, R38.1, R39.1, R40.1

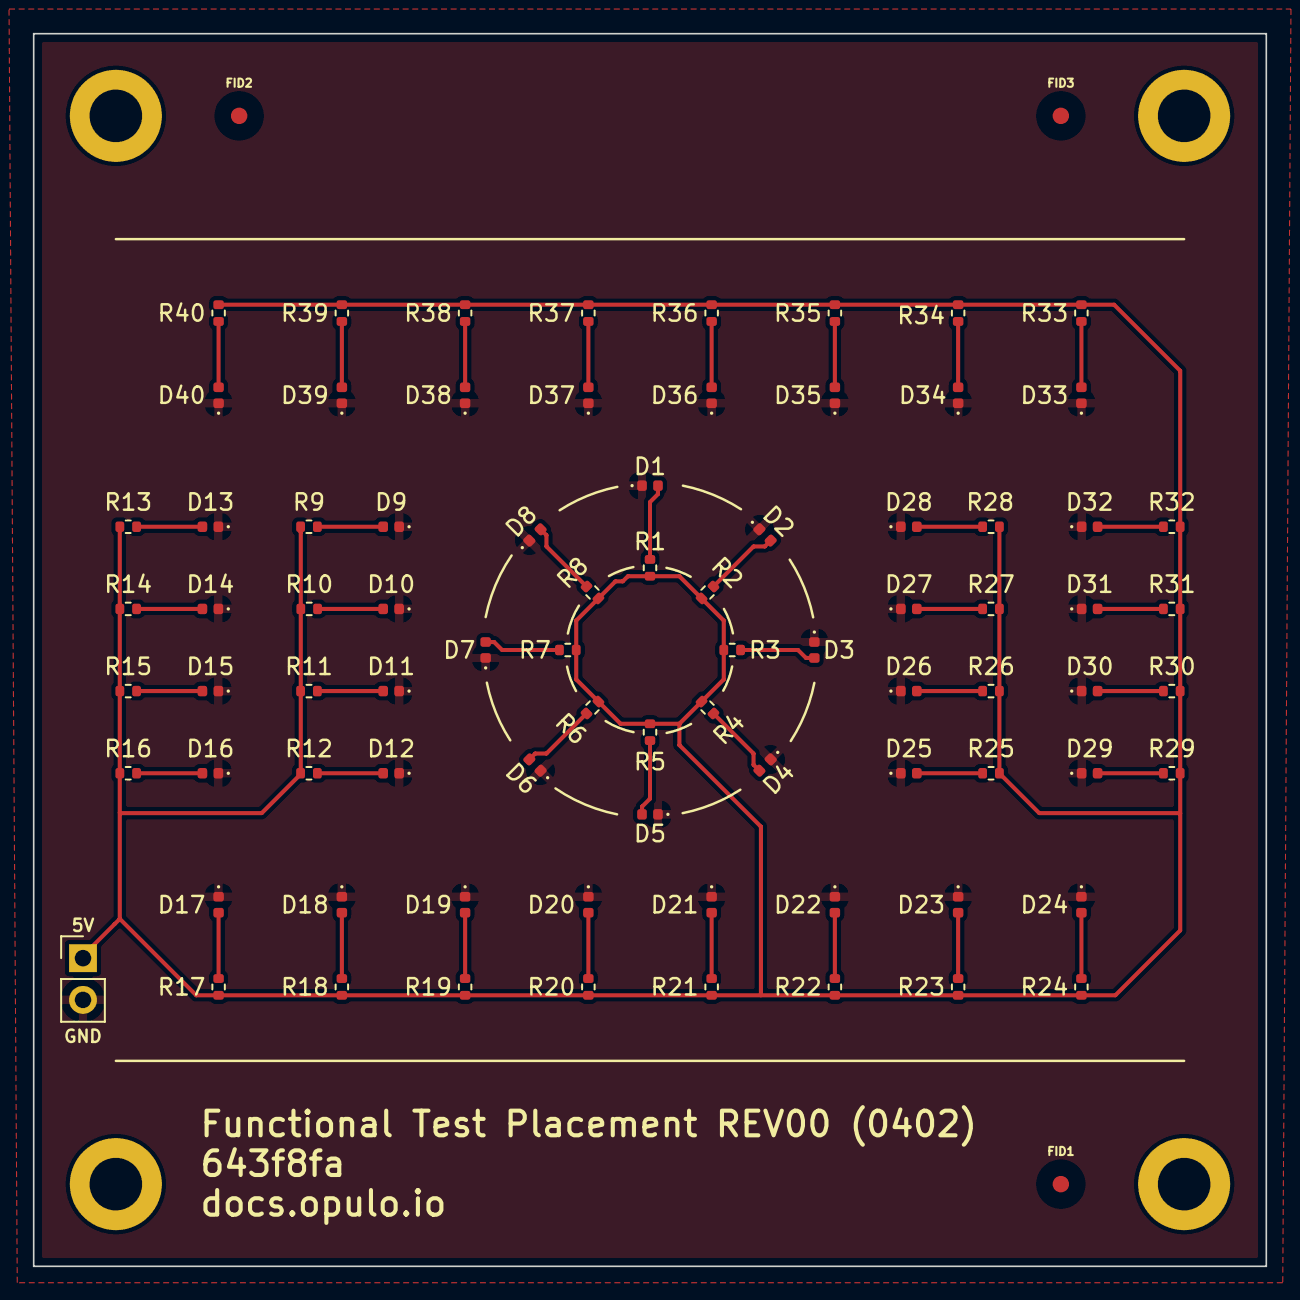
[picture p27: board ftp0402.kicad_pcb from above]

Board: 2 copper layers, 75.0 x 75.0 mm, 90 parts (1 on the bottom side), 42 nets.

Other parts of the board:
G1: LOGO; opulo-logo
G2: LOGO; cal-dot-grid

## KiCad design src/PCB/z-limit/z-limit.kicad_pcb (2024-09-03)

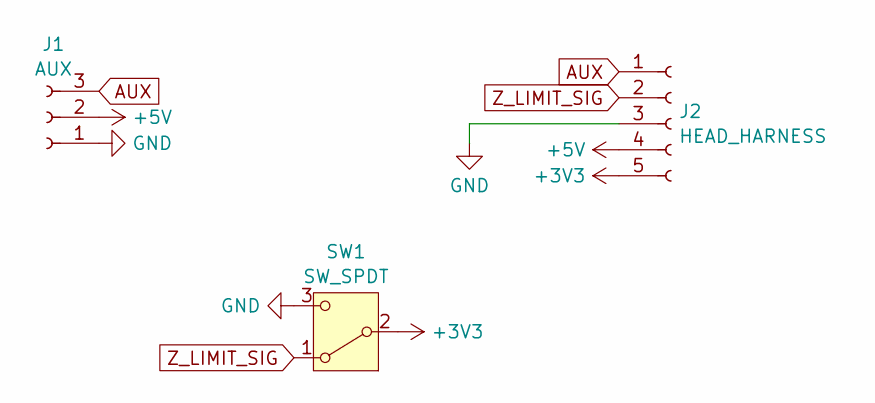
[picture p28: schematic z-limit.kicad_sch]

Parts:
J1: AUX; JST_PH_S3B-PH-K_1x03_P2.00mm_Horizontal; MFG Part Number S3B-PH-K-S(LF)(SN); LCSC Part Number C157929
J2: HEAD_HARNESS; JST_PH_B5B-PH-SM4-TB_1x05-1MP_P2.00mm_Vertical; MFG Part Number HC-PH-5ALT; LCSC Part Number C2845454
SW1: SW_SPDT; D2FS-FL-N-A; MFG Part Number DM1-12UC-1; LCSC Part Number C466018

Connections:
+3V3: J2.5, SW1.2 (B)
+5V: J1.2, J2.4
AUX: J1.3, J2.1
GND: J1.1, J2.3, J2.MP, SW1.3 (C)
Z_LIMIT_SIG: J2.2, SW1.1 (A)

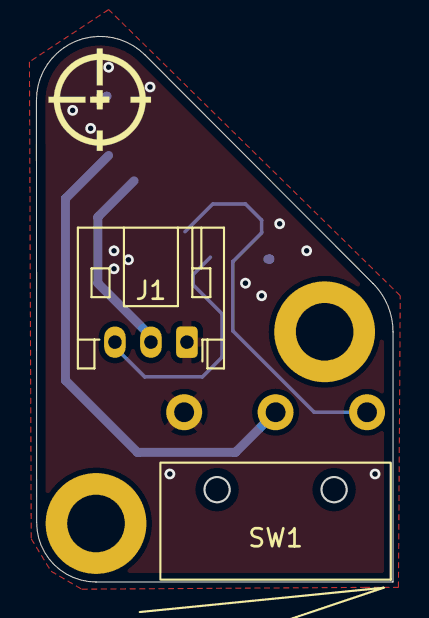
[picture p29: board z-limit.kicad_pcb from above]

Board: 2 copper layers, 19.8 x 30.3 mm, 3 parts (1 on the bottom side), 5 nets.

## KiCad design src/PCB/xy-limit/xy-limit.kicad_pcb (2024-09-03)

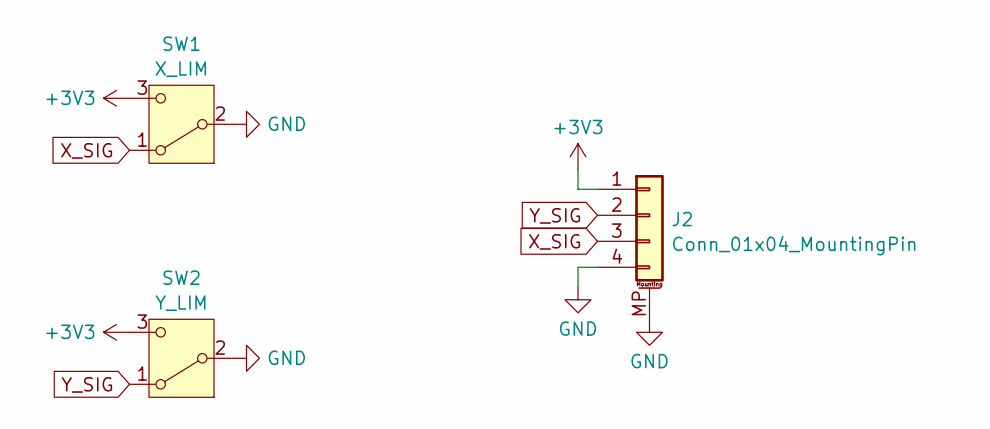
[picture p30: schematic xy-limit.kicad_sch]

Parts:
J2: Conn_01x04_MountingPin; JST_PH_B4B-PH-SM4-TB_1x04-1MP_P2.00mm_Vertical; MFG Part Number HC-PH-4ALT; LCSC Part Number C2845453
SW1: X_LIM; D2FS-FL-N-A; MFG Part Number DM1-12UC-1; LCSC Part Number C466018
SW2: Y_LIM; D2FS-FL-N; MFG Part Number DM1-135P-1; LCSC Part Number C405946

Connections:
+3V3: J2.1, SW1.3 (C), SW2.3 (C)
GND: J2.4, J2.MP (MountPin), SW1.2 (B), SW2.2 (B)
X_SIG: J2.3, SW1.1 (A)
Y_SIG: J2.2, SW2.1 (A)

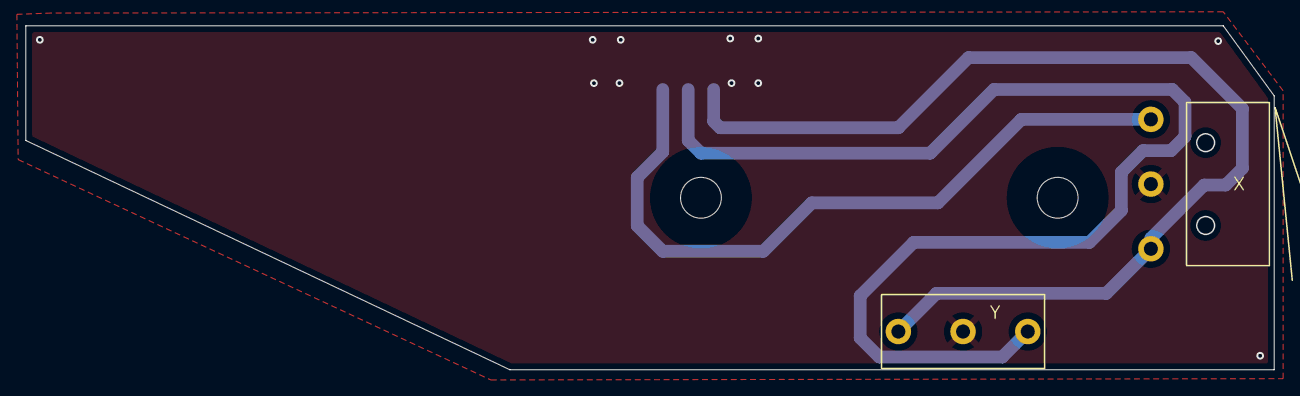
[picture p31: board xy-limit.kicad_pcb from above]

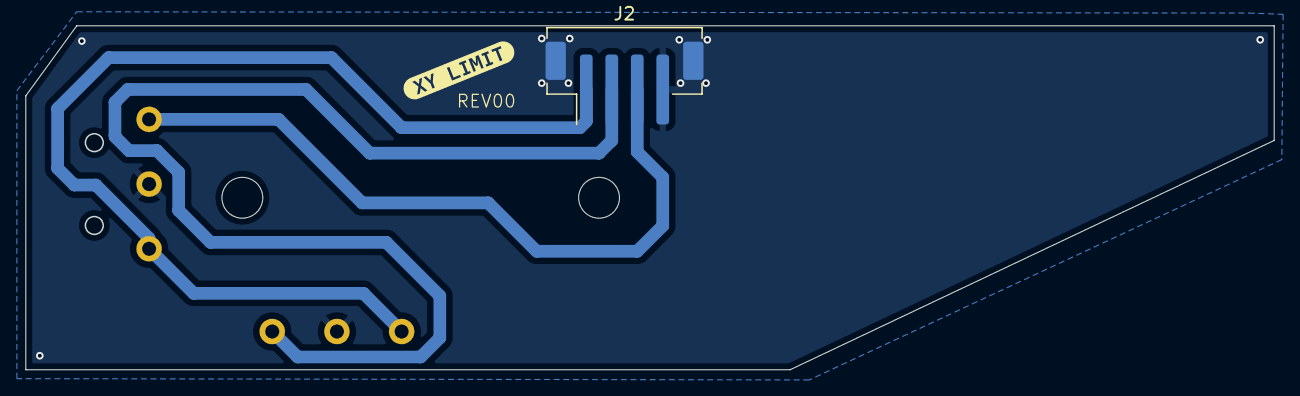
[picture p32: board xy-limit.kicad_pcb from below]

Board: 2 copper layers, 98.0 x 27.0 mm, 4 parts (2 on the bottom side), 4 nets.

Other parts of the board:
kibuzzard-65F47CEB: G***; kibuzzard-65F47CEB

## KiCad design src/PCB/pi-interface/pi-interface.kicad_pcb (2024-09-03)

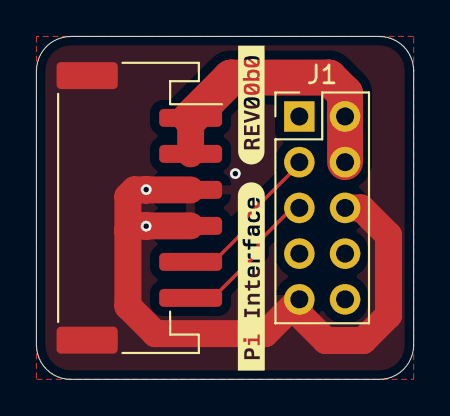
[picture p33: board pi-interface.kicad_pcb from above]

Board: 2 copper layers, 21.0 x 19.1 mm, 4 parts (0 on the bottom side), 4 nets.

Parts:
J1: PI; PinHeader_2x05_P2.54mm_Vertical
Je: MOBO; JST_PH_S6B-PH-SM4-TB_1x06-1MP_P2.00mm_Horizontal
kibuzzard-6647A66F: G***; kibuzzard-6647A66F
kibuzzard-6647A648: G***; kibuzzard-6647A648

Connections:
+5V: J1.2, J1.4, Je.1, Je.2
BOOT: J1.3, Je.5
GND: J1.6, J1.9, Je.3, Je.4, Je.MP (MountPin)
RESET: J1.5, Je.6

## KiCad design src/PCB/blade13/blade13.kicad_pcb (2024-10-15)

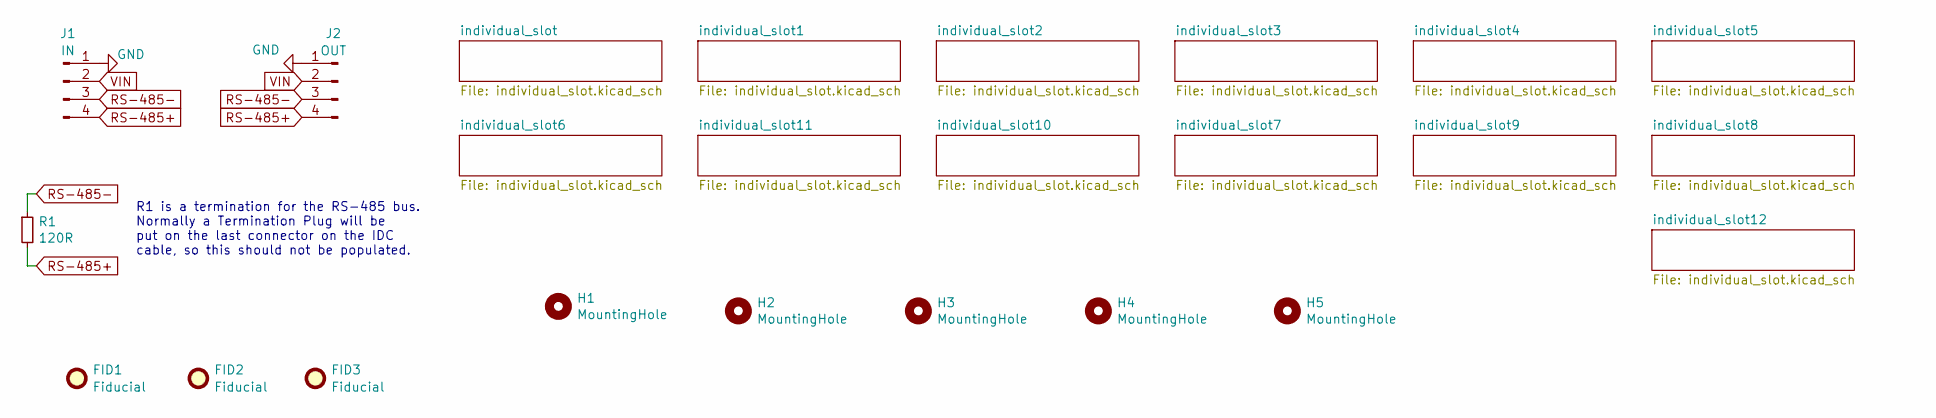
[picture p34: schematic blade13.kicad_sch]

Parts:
FID1, FID2, FID3: Fiducial; Fiducial_1mm_Mask2mm
H1, H2, H3, H4, H5: MountingHole; MountingHole_3.2mm_M3
J1: IN; JST_PH_B4B-PH-SM4-TB_1x04-1MP_P2.00mm_Vertical
J2: OUT; JST_PH_B4B-PH-SM4-TB_1x04-1MP_P2.00mm_Vertical
R1: 120R; R_0805_2012Metric; JLCPCB C17437

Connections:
GND: J1.1, J1.MP, J2.1, J2.MP; also elsewhere on the board
RS-485+: J1.4, J2.4, R1.2; also elsewhere on the board
RS-485-: J1.3, J2.3, R1.1; also elsewhere on the board
VIN: J1.2, J2.2; also elsewhere on the board

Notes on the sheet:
R1 is a termination for the RS-485 bus. Normally a Termination Plug will be put on the last connector on the IDC cable, so this should not be populated.

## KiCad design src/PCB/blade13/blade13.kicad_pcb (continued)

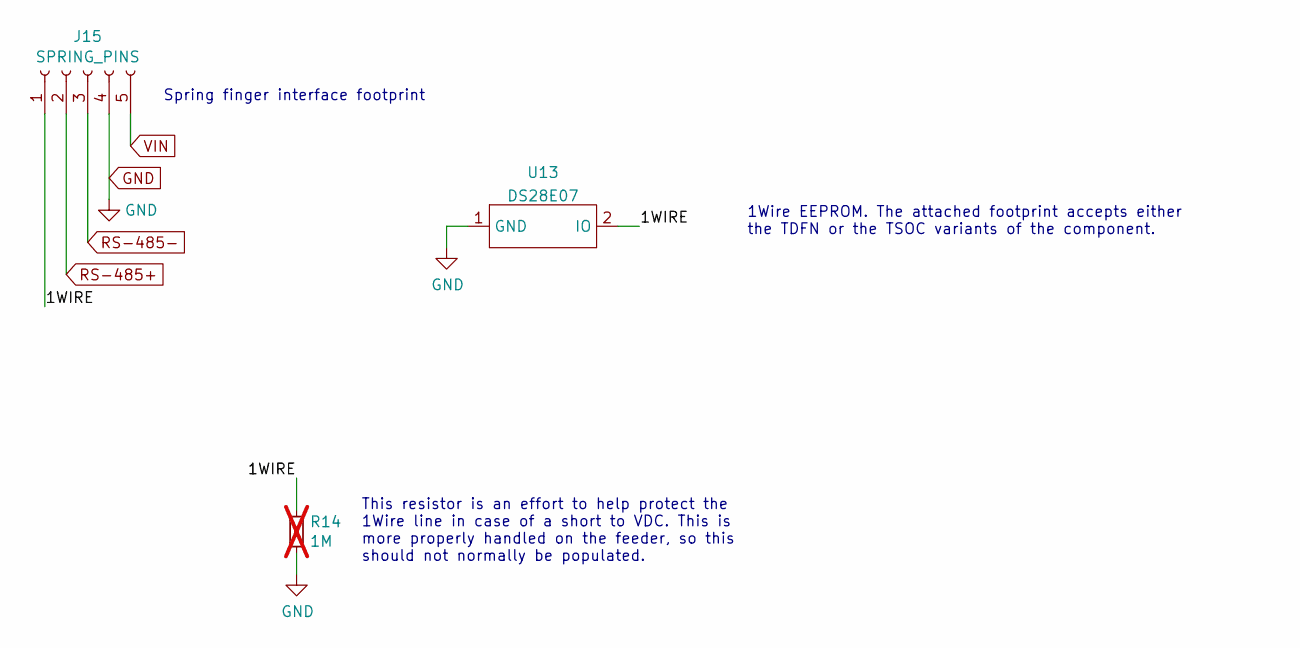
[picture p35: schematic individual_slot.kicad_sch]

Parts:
J15: SPRING_PINS; AVX-915-005-541-Contact-Surface
R14: 1M; R_0805_2012Metric; JLCPCB C17437; not fitted
U13: DS28E07; DS28E07_MULTI

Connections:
/individual_slot12/1WIRE: J15.1, R14.1, U13.2 (IO)
GND: J15.4, R14.2, U13.1 (GND); also elsewhere on the board
RS-485+: J15.2; also elsewhere on the board
RS-485-: J15.3; also elsewhere on the board
VIN: J15.5; also elsewhere on the board

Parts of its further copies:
J3, J4, J5, J6, J7, J8, J9, J10, J11, J12, J13, J14: SPRING_PINS; AVX-915-005-541-Contact-Surface
R2, R3, R4, R5, R6, R7, R8, R9, R10, R11, R12, R13: 1M; R_0805_2012Metric; JLCPCB C17437; not fitted
U1, U2, U3, U4, U5, U6, U7, U8, U9, U10, U11, U12: DS28E07; DS28E07_MULTI

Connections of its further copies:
/individual_slot1/1WIRE: J4.1, R3.1, U2.2 (IO)
/individual_slot2/1WIRE: J5.1, R4.1, U3.2 (IO)
/individual_slot3/1WIRE: J6.1, R5.1, U4.2 (IO)
/individual_slot4/1WIRE: J7.1, R6.1, U5.2 (IO)
/individual_slot5/1WIRE: J8.1, R7.1, U6.2 (IO)
/individual_slot6/1WIRE: J9.1, R8.1, U7.2 (IO)
/individual_slot7/1WIRE: J10.1, R9.1, U8.2 (IO)
/individual_slot8/1WIRE: J11.1, R10.1, U9.2 (IO)
/individual_slot9/1WIRE: J12.1, R11.1, U10.2 (IO)
/individual_slot10/1WIRE: J13.1, R12.1, U11.2 (IO)
/individual_slot11/1WIRE: J14.1, R13.1, U12.2 (IO)
/individual_slot/1WIRE: J3.1, R2.1, U1.2 (IO)
GND: J3.4, J4.4, J5.4, J6.4, J7.4, J8.4, J9.4, J10.4, J11.4, J12.4, J13.4, J14.4, R2.2, R3.2, R4.2, R5.2, R6.2, R7.2, R8.2, R9.2, R10.2, R11.2, R12.2, R13.2, U1.1 (GND), U2.1 (GND), U3.1 (GND), U4.1 (GND), U5.1 (GND), U6.1 (GND), U7.1 (GND), U8.1 (GND), U9.1 (GND), U10.1 (GND), U11.1 (GND), U12.1 (GND); also elsewhere on the board
RS-485+: J3.2, J4.2, J5.2, J6.2, J7.2, J8.2, J9.2, J10.2, J11.2, J12.2, J13.2, J14.2; also elsewhere on the board
RS-485-: J3.3, J4.3, J5.3, J6.3, J7.3, J8.3, J9.3, J10.3, J11.3, J12.3, J13.3, J14.3; also elsewhere on the board
VIN: J3.5, J4.5, J5.5, J6.5, J7.5, J8.5, J9.5, J10.5, J11.5, J12.5, J13.5, J14.5; also elsewhere on the board

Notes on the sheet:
This resistor is an effort to help protect the 1Wire line in case of a short to VDC. This is more properly handled on the feeder, so this should not normally be populated.
Spring finger interface footprint
1Wire EEPROM. The attached footprint accepts either the TDFN or the TSOC variants of the component.



Board: 2 copper layers, 203.0 x 26.6 mm, 53 parts (13 on the bottom side), 17 nets.

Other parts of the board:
kibuzzard-65FDDA45: G***; kibuzzard-65FDDA45
kibuzzard-65FDDA59: G***; kibuzzard-65FDDA59
kibuzzard-65FDDA61: G***; kibuzzard-65FDDA61

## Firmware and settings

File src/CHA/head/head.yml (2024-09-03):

connectors:

  X:
    style: simple
    autogenerate: true
    type: ""
    ignore_in_bom: true

# Z Motor 
  ZM-M:
    pinlabels: [A, B, C, D] # pincount implicit in pinout
    type: JST PH
    subtype: female
    image:
      src: ../img/PH-4.jpeg
      caption: JST PH 4-pin

  ZM-H:
    pinlabels: [A, B, C, D, E, F] # pincount implicit in pinout
    type: JST PH
    subtype: female
    image:
      src: ../img/PH-6.jpeg
      caption: JST PH 6-pin

# L Motor 
  LM-M:
    pinlabels: [A, B, C, D] # pincount implicit in pinout
    type: JST PH
    subtype: female
    image:
      src: ../img/PH-4.jpeg
      caption: JST PH 4-pin

  LM-H:
    pinlabels: [A, B, C, D, E, F] # pincount implicit in pinout
    type: Molex 51065-0600
    subtype: female
    image:
      src: ../img/molex-51065-0600.png
      caption: Molex 51065 0600
      height: 70

# R Motor 
  RM-M:
    pinlabels: [A, B, C, D] # pincount implicit in pinout
    type: JST PH
    subtype: female
    image:
      src: ../img/PH-4.jpeg
      caption: JST PH 4-pin

  RM-H:
    pinlabels: [A, B, C, D, E, F] # pincount implicit in pinout
    type: Molex 51065-0600
    subtype: female
    image:
      src: ../img/molex-51065-0600.png
      caption: Molex 51065 0600
      height: 70

# Z Limit
  ZL-M:
    pinlabels: [AUX, Z_LIMIT, GND, 5V, 3V3] # pincount implicit in pinout
    type: JST PH
    subtype: female
    image:
      src: ../img/PH-5.jpeg
      caption: JST PH 5-pin

  ZL-H:
    pinlabels: [AUX, Z_LIMIT, GND, 5V, 3V3] # pincount implicit in pinout
    type: JST PH
    subtype: female
    image:
      src: ../img/PH-5.jpeg
      caption: JST PH 5-pin

# Top Light
  TL-M:
    pinlabels: [SIG, VCC, GND] # pincount implicit in pinout
    type: JST PH
    subtype: female
    image:
      src: ../img/PH-3.jpeg
      caption: JST PH 3-pin

  TL-H:
    pinlabels: [SIG, VCC, GND] # pincount implicit in pinout
    type: JST XH
    subtype: female
    image:
      src: ../img/XH-3.jpeg
      caption: JST XH 3-pin

cables:
  W1:
    wirecount: 20
    length: 1.57
    gauge: 24 AWG
    show_equiv: true
    colors: [WH, RD, YE, BK, WH, RD, YE, BK, WH, RD, YE, BK, WH, RD, YE, BK, WH, WH, RD, YE]
    notes:  Stranded - All Black PVC Insulation

  ZM-M-CABLE:
    wirecount: 4
    length: 0.1
    category: bundle
    gauge: 0
    show_equiv: true
    colors: [WH, RD, YE, BK]
    notes:  ""
    image:
      src: ../img/label.png
      caption: Label Text "Z MOTOR"
      height: 100

  ZM-H-CABLE:
    wirecount: 4
    length: 0.13
    category: bundle
    gauge: 0
    show_equiv: true
    colors: [WH, RD, YE, BK]
    notes:  ""
    image:
      src: ../img/label.png
      caption: Label Text "Z MOTOR"
      height: 100

  LM-M-CABLE:
    wirecount: 4
    length: 0.1
    category: bundle
    gauge: 0
    show_equiv: true
    colors: [WH, RD, YE, BK]
    notes:  ""
    image:
      src: ../img/label.png
      caption: Label Text "L MOTOR"
      height: 100

  LM-H-CABLE:
    wirecount: 4
    length: 0.3
    category: bundle
    gauge: 0
    show_equiv: true
    colors: [WH, RD, YE, BK]
    notes:  ""
    image:
      src: ../img/label-red.png
      caption: Label Text "L MOTOR"
      height: 100

  RM-M-CABLE:
    wirecount: 4
    length: 0.1
    category: bundle
    gauge: 0
    show_equiv: true
    colors: [WH, RD, YE, BK]
    notes:  ""
    image:
      src: ../img/label.png
      caption: Label Text "R MOTOR"
      height: 100

  RM-H-CABLE:
    wirecount: 4
    length: 0.3
    category: bundle
    gauge: 0
    show_equiv: true
    colors: [WH, RD, YE, BK]
    notes:  ""
    image:
      src: ../img/label-blue.png
      caption: Label Text "R MOTOR"
      height: 100

  ZL-M-CABLE:
    wirecount: 5
    length: 0.14
    category: bundle
    gauge: 0
    show_equiv: true
    colors: [WH, RD, YE, BK, WH]
    notes:  ""
    image:
      src: ../img/label.png
      caption: Label Text "Z LIMIT"
      height: 100

  ZL-H-CABLE:
    wirecount: 5
    length: 0.12
    category: bundle
    gauge: 0
    show_equiv: true
    colors: [WH, RD, YE, BK, WH]
    notes:  ""
    image:
      src: ../img/label.png
      caption: Label Text "Z LIMIT"
      height: 100

  TL-M-CABLE:
    wirecount: 3
    length: 0.17
    category: bundle
    gauge: 0
    show_equiv: true
    colors: [WH, RD, YE]
    notes:  ""
    image:
      src: ../img/label.png
      caption: Label Text "TOP LIGHT"
      height: 100

  TL-H-CABLE:
    wirecount: 3
    length: 0.15
    category: bundle
    gauge: 0
    show_equiv: true
    colors: [WH, RD, YE]
    notes:  ""
    image:
      src: ../img/label.png
      caption: Label Text "TOP LIGHT"
      height: 100


connections:

# Z Motor
  -
    - ZM-M: [1-4]
    - ZM-M-CABLE: [1-4]
    - [X, X, X, X]
    - W1: [1-4]
    - [X, X, X, X]
    - ZM-H-CABLE: [1-4]
    - ZM-H: [1,4,3,6]
    

# L Motor
  -
    - LM-M: [1-4]
    - LM-M-CABLE: [1-4]
    - [X, X, X, X]
    - W1: [5-8]
    - [X, X, X, X]
    - LM-H-CABLE: [1-4]
    - LM-H: [1,4,3,6]
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

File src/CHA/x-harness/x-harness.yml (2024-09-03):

connectors:

  X:
    style: simple
    autogenerate: true
    type: ""
    ignore_in_bom: true
    

  XM-M:
    pinlabels: [A, B, C, D] # pincount implicit in pinout
    type: JST PH
    subtype: female
    image:
      src: ../img/PH-4.jpeg
      caption: JST PH 4-pin

  XYL-M:
    pinlabels: [3V3, Y_SIG, X_SIG, GND] # pincount implicit in pinout
    type: JST PH
    subtype: female
    image:
      src: ../img/PH-4.jpeg
      caption: JST PH 4-pin

  XM-H:
    pinlabels: [A, B, C, D, E, F] # pincount implicit in pinout
    type: JST PH
    subtype: female
    image:
      src: ../img/PH-6.jpeg
      caption: JST PH 6-pin

  XYL-H:
    pinlabels: [3V3, Y_SIG, X_SIG, GND] # pincount implicit in pinout
    type: JST PH
    subtype: female
    image:
      src: ../img/PH-4.jpeg
      caption: JST PH 4-pin

cables:
  W1:
    wirecount: 8
    length: 0.72
    gauge: 24 AWG
    show_equiv: true
    colors: [WH, RD, YE, BK, RD, BU, YE, BK]
    notes:  Stranded - All Black PVC Insulation
    

  XM-M-CABLE:
    wirecount: 4
    length: 0.05
    category: bundle
    gauge: 24 AWG
    show_equiv: true
    colors: [WH, RD, YE, BK]
    notes: ""
    image:
      src: ../img/label.png
      caption: Label Text "X MOTOR"
      height: 100

  XM-H-CABLE:
    wirecount: 4
    length: 0.1
    category: bundle
    gauge: 24 AWG
    show_equiv: true
    colors: [WH, RD, YE, BK]
    notes: ""
    image:
      src: ../img/label.png
      caption: Label Text "X MOTOR"
      height: 100

  XYL-M-CABLE:
    wirecount: 4
    length: 0.17
    category: bundle
    gauge: 24 AWG
    show_equiv: true
    colors: [RD, BU, YE, BK]
    notes: ""
    image:
      src: ../img/label.png
      caption: Label Text "XY LIMIT"
      height: 100

  XYL-H-CABLE:
    wirecount: 4
    length: 0.13
    category: bundle
    gauge: 24 AWG
    show_equiv: true
    colors: [RD, BU, YE, BK]
    notes: ""
    image:
      src: ../img/label.png
      caption: Label Text "XY LIMIT"
      height: 100

connections:
  -
    - XM-M: [1-4]
    - XM-M-CABLE: [1-4]
    - [X, X, X, X]
    - W1: [1-4]
    - [X, X, X, X]
    - XM-H-CABLE: [1-4]
    - XM-H: [1,4,3,6]
  -
    - XYL-M: [1-4]
    - XYL-M-CABLE: [1-4]
    - [X, X, X, X]
    - W1: [5-8]
    - [X, X, X, X]
    - XYL-H-CABLE: [1-4]
    - XYL-H: [1-4]

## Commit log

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2022-06-13 fixes old repo reference in exporting csm and bom CI scripts
2022-06-13 fixes some bom image links and amounts
    [bom.csv]
2022-06-14 fixes zipping of images for webpage bom on releases
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2022-06-16 fixes jumper 2 having the incorrect footprint for stepper driver config. footprint name said 23 but 13 was connected
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2022-06-17 adds custom combo power jack footprint for both barrel jack and terminal block
    [mobo.kicad_sch, power.kicad_sch, single_motor.kicad_sch]
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2022-06-17 attempts to fix AssertionError in foot.FCStd
    [foot.FCStd]
2022-06-19 creates v3 branch for lumenpnp CAD enhancements
    - implements a removable x-gantry
    - adds support for xy drag chain
    - reintroduces a center foot to the staging plate
    - restructures the hierarchy of the CAD assembly
    - flips the y-axis stepper motors upside down to reduce machine footprint
    [back-left-leg.FCStd, back-leg.FCStd, back-right-leg.FCStd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]
2022-06-19 removes umbilical components from FDM folder
    removes currently vestigial umbilical components from V3 source
    [frame-umbilical-mount.FCStd, umbilical-swivel-extension.FCStd, umbilical-swivel.FCStd]
2022-06-21 Updates machine to dual toolhead with auxiliary staging plate
    - adds additional CP40 holder, NEMA 11 motor, 24v pump, solenoid, pump mount, pneumatic fittings, and misc. fasteners to assembly
    - adds auxiliary staging plate to assembly
    - adds CAD of staging-plate w/removable cover plate for camera cutout to repo
    - adds simplified 2-piece foot assembly for use with an auxiliary staging-plate
    - adds raised bosses to x-idler-mount to remove need for washers when attaching component to y-gantry with m5x25 bolts
    [extended-foot.FCStd, staging-plate.STEP, x-idler-mount.FCStd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]
2022-06-27 Updates orientation of CAD models within the assembly
    Fixes the assembly being at a weird angle
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2022-07-05 edits some USB stuff. trying a system where the hub is not present, and the board acts as a passthrough and power supply for the bottom camera, and the top is connected directly.
    [mobo.kicad_sch, mosfet.kicad_sch, power.kicad_sch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]
2022-07-05 adds usb type b port to test for strength of connection to pcb
    [mobo.kicad_sch, single_motor.kicad_sch, usb.kicad_sch]
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2022-07-13 Addresses CAD issues and misc. improvements
    - Closes #582 [FDM-0017 friction on screw head] and mitigate potential collisions with Z-Idler by adding chamfers to bottom edges of Z-Gantry-left/right to address
    - Closes #583 [FDM-0011-02 height of the idle pulley] by raising idler pulley mounting surface up 0.25mm
    - Closes #581 [Rear Legs have structural weakness at lower 2020 extrusion socket] by widening 2020 pockets by 0.2mm (now 20.2mm x 20.2mm)
    - Consolidates back-left-leg and back-right-leg into a single symmetrical component named back-leg
    - Adds optional extended-foot part to BOM for use with additional staging plates
    [back-left-leg.FCStd, back-leg.FCStd, back-right-leg.FCStd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]
2022-07-13 Update bom.csv
    Adds notes on attachment hardware for additional staging plate foot-mounts
    [bom.csv]
2022-07-14 adds fuse, esd protection to USB lines, removes usb hub, switches to chonky usb type b
    [dual_motors.kicad_sch, mobo.kicad_sch, power.kicad_sch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]
2022-07-14 removes feeder stuff from main repo so we can put it in a separate one
    [assembly.FCStd, drive-motor-mount.FCStd, feeder-floor-pcb.FCStd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]
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2022-07-19 removes passthrough usb connectors, cleans up lots of routing, rearranges i2c multiplexer and passives, adds vacuum tubing strain relief cutout
    [mobo.kicad_sch, mosfet.kicad_sch, single_motor.kicad_sch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]
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2022-07-22 Continues work on LumenPnP v3 CAD development
    Nozzle Storage Improvements:
    - Updates nozzle-rack to add support for mounting component horizontally in the center of a staging-plate
    - Updates nozzle-rack to add clearance for possible neighboring M3 hardware on a staging-plate
    Porting improvements from v2 branch to readdress the following issues (see commit e80a7d5 for details):
    - #583 [FDM-0011-02 height of the idle pulley] by raising idler pulley mounting surface up 0.25mm for v3 LumenPnP branch
    - #582 [FDM-0017 friction on screw head] and mitigate potential collisions with Z-Idler by adding chamfers to bottom edges of z-gantry for v3 LumenPnP branch
    - #581 [Rear Legs have structural weakne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
    [allen-wrench-holder.FCStd, back-leg.FCStd, bottom-camera-cover.FCStd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]
2022-07-28 Continued work on v3 CAD improvements
    - Removes Y-Limit Switch and related mounting features on front-left-leg and front-right-leg
    - Increases wall thickness of ringlight shroud feature on bottom-light-mount from 1mm to 1.25mm
    - Updates front-drag-chain-mount to angle drag chain by 5 degrees
    - Updates front-drag-chain-mount to bolt onto side of front-left-leg rather than on the front face with embedded hex nuts
    - Removes asymmetrical z-gantry components from FDM folder
    - Introduces x-motor-cable-guide for use with managing the x-motor cable as it leaves the drag chain assembly
    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
    [bottom-light-mount.FCStd, front-drag-chain-mount.FCStd, front-left-leg.FCStd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]
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2022-08-01 small silkscreen fixes, adds bottom light pcb mount
2022-08-01 fixes some library and ERC issues
    [dual_motors.kicad_sch, mosfet.kicad_sch, power.kicad_sch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]
2022-08-01 tries to fix kibot index out of range error by importing from schematic to pcb
2022-08-01 fixes some libarry messiness that might be causing the errors with kibot in the ci
    [dual_motors.kicad_sch, single_motor.kicad_sch, usb.kicad_sch]
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2022-08-02 replaces SRL05 for SRV05 due to pricing and availability, routed mostfet gate resistors and added 2g34 buffer to boost the voltage of the servo drive pins. consolidated a random cap value that could 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
    [dual_motors.kicad_sch, microcontroller.kicad_sch, mobo.kicad_sch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]
2022-08-02 Updates CAD for test production run
    - Updates bom.csv to include wire harnesses and all other v3 component changes
    - Removes x-limit and y-limit cables from BOM
    - Renames l-motor-harness to toolhead-motor-harness in preparation for use with dual toolhead machines
    - Updates motherboard ECAD to rev 4
    - Updates y-gantry to support the detachable x-gantry design
    - Updates front-drag-chain-mount to reduce form factor and mounting technique
    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
    [8mm-strip-feeder.FCStd, bom.csv, bottom-camera-cover.FCStd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]
2022-08-02 Updates CAD to fix issues found during Github Action Run #7638671591
    - Renames main body of static-camera-foot model from Body001 to Body
    - Renames print plane on x-gantry-back from PrintPlane001 to PrintPlane
    - Adds missing print plane to valve-mount
    - Adds missing print plane to extended-foot
    - Adds missing print plane to allen-wrench-holder
    - Adds missing print plane to board-support
    - Adds missing print plane to board-mount-dynamic
    - Adds missing print plane to board-mount-static
    [allen-wrench-holder.FCStd, board-mount-dynamic.FCStd, board-mount-static.FCStd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]
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2022-08-02 Updates bom.csv for minor issues
    - Adds allen-wrench-holder to BOM as optional part
    - Adds squaring-bracket to BOM as optional part
    - Updates list order of BOM to improve organization
    - Adds a source for usb-b-to-usb-a-cable to BOM
    [bom.csv]
2022-08-02 Fixes BOM link issue and minor assembly order change
    [bom.csv]
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2022-08-09 fixes some silkscreen errors
2022-08-11 Adds further BOM detail and improves auxiliary staging plate foot
    - Adds print plane to front-right-leg
    - Simplifies aux staging plate design from 2 prints and 8 fasteners to 3 total pieces
    - Updates assembly to match changes listed above
    - Updates BOM to bring it into alignment with Opulo MFG sourcing data
    [aux-staging-plate-foot.FCStd, bom.csv, front-right-leg.FCStd]
2022-08-15 Updates 8mm feeder for design improvements
    Makes the flexy bit of the feeder stronger and fit paper and plastic tape better
    [8mm-strip-feeder.FCStd]
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2022-08-21 Updates FDM models to improve mid-air holes
    Improves the way holes that interrupt bridged surfaces are printed using Vector 3D's bridging hole perimeters technique
    [front-left-leg.FCStd, front-right-leg.FCStd, y-gantry-support.FCStd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]
2022-08-22 Cont. V3 CAD Improvements
    - Removed old stye aux-staging-plate support foot accidentally left in assembly file
    - Creates additional THT components for mobo-rev04 CAD in preparation for mobo-top-cover improvements
    - Pushes mobo CAD enhancements to the assembly file
    [C9136-Shorter-Leads.FCStd, Fuse_Holder_3568.FCStd, Mini-Blade-Fuse.FCStd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]
2022-08-24 Improves X-Gantry-Front
    - Added backside chamfer to X-Gantry-Front to remove risk of elephants foot
    - Added linear rail alignment features to X-Gantry-Front to aid in assembly of toolhead
    [x-gantry-front.FCStd]
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2022-09-07 Stages CAD for production release candidate
    - Updates hex pocket on peek-cable-clamp for press-fit M3 hex nuts
    - Adds chamfers to peek-cable-clamp to avoid hard edges pressing into cables when clamping
    - Adds linear-rail locating features to x-gantry-front
    - Adds raised jumper pins to TMC stepper driver CAD for reference when designing cover plates
    - Flips location of bottom-ring-light cable passthrough slot on mobo-bottom-cover
    - Updates mobo-top-cover design to include flexible section for pressing buttons on motherboard
    - Flips PrintPlane on belt-clamp so teeth print against build plate with bridging
    - Shortens z-gantry to add 13mm z-clearance
    - Increases height of nozzle-rack for support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
    [TMC2209-V3_0.FCStd, belt-clamp.FCStd, bom.csv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]
2022-09-13 Last minute changes before production
    - Introduces y-coupler-bracket for mounting y-couplers to staging-plate
    - Updates BOM.CSV for the respective fastener changes caused by the introduction of y-coupler-bracket
    - Fixes CI build issue on mobo-top-cover by renaming Body003 to Body
    - Adds hidden letters denoting L & R on valve-mount to indicate which valve goes where
    - Introduces major changes to the nozzle-rack, adding internal flexure features for securing the N75 nozzle
    - Moves nozzle-rack back to it's original location on the staging-plate, in order 1) reduce staging-plate bowing during nozzle-change 2) reduce likelihood of collisions when traveling between WIP PCBs and powered feeders
    [bom.csv, mobo-top-cover.FCStd, valve-mount.FCStd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]
2022-09-14 Addresses issues seen in compiled v3 release candidate BOM
    - Fixes broken images in BOM
    - Removes reference to extended-foot
    [bom.csv, extended-foot.FCStd]
2022-09-14 Yet another minor patch to BOM.CSV before production release
    - Corrects incorrect QTY of fasteners needed to mount 8mm-strip-feeder
    - Corrects the listed device ID for ELP-USB100W03M-L60-Bottom
    - Updates BOM to list the actual QTY of zip-ties required for a LumenPnP
    - Updates BOM to list the actual required length of GT2 belt for X & Y axes
    - Makes verbiage in comments column more consistent
    [bom.csv]
2022-09-15 Removes old FDM part and minor cleanup to assembly file
    - removed foot-mount for FDM folder
    - adjusted position of several components in assembly file
    - unhid feeder-rails
    [foot-mount.FCStd]
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2022-10-13 Continued CAD Improvements
    Tolerance Updates
    - Updates hex pocket on y-gantry-support for looser fit
    - Raised "GT2 Rest Pad" on y-gantry upward by 0.25mm to prevent feature from rubbing on 2020 v-groove channel
    - Tightened pockets on allen-wrench-holder to hold wrenches better
    - Deepened M5 counterbores on y-gantry by 0.8mm to keep bolts flush with print plane surface and prevent collision with x-gantry
    - Deepened M5 hex nut pockets on y-gantry-support by 0.8mm to create additional thread engagement with M5x40 bolts
    - Loosened and rotated hex nut pocket on y-coupler-bracket to prevent print splitting during hex nut installation
    Z-Limit Switch Improvements / Fastener Changes
    - Moved limit sw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
    [allen-wrench-holder.FCStd, bom.csv, y-coupler-bracket.FCStd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]
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2022-11-07 Continued mechanical improvements
    - corrected nozzle-rack mounting bolts to be m3x10 rather than m3x8
    - fixed bom.csv to have correct number of m3x10 button head bolt
    - closed #600 by thinning out bottom-light-mount and extending bottom-camera-mount
    - flipped lettering on y-coupler-bracket to avoid needing to twist pneumatic tubes when entering into the motherboard
    - updated extrusion-cable-clip to support printing with a 0.6mm nozzle
    - updated usb-camera.FCStd to show the correct location of the focus lock screw
    [bom.csv, extrusion-cable-clip.FCStd, top-camera-mount.FCStd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]
2022-11-07 updated tolerances
    widened and deepened m2.5 mounting holes on top-light-mount
    [top-light-mount.FCStd]
2022-11-07 Fixes BOM to have correct length of pneumatic-tubing-6mmOD
    - adds 0.095m pneumatic-tubing-6mmOD to BOM
    [bom.csv]
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2023-02-17 Applies DFAM to mobo-top-cover
    - Updates mobo-top-cover to increase boot/reset font size
    - Updates mobo-top-cover to remove the tiny slots previously required for TMC2209 aux pin header
    [mobo-top-cover.FCStd]
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2023-05-08 commits lumenpnp linear rail mod for engineering evaluation
    - merges the LumenPnP linear rail by @theacodes into cag-staging
    - See https://github.com/theacodes/3d-prints/tree/75257a3e946579d3280ea832feeb0a32f24e6ff6/lumen/linear%20rail%20mod%20(v3)
    - Cleans up source files for missing fasteners and misaligned geometry
    [500mm-MGN12H001.FCStd, 550mm-MGN12H001.FCStd, M3-tslot-nut.FCStd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]
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2023-05-12 uses more recent build of the kicad7 container that fixes a bug with rendering polygons
2023-05-12 replaces polygon edge cuts outline of ftp with lines to work around pcbdraw rendering bug
    [ftp.kicad_pcb]
2023-05-15 fixes #622
    [bom.csv]
2023-05-15 fixes #380
    [bom.csv]
2023-05-31 x-toolhead-asm electronics improvements
    - Adds WIP top-camera-cover to protect exposed top-camera PCB
    - This cover still requires raised protrusions to space it away and prevent collisions with the SMT components on the PCB
    - Adds new region to top-light-cover to cover exposed top-ring-light THT pins
    - Rotates toolhead motors 90º to reduce cable strain
    - Adds notch in z-gantry to create clearance for nema-11 toolhead motor
    - Adds zip tie channel in z-gantry to create cable strain relief point for L/R toolhead cable
    [top-light-mount.FCStd, z-gantry.FCStd]
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2023-06-20 adds missing footprint for vacuum sensor
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2023-07-27 Continued cad enhancements for v3.1.0
    - Adds 525mm T-Nut-Bar to x and y gantry
    - Updates front-drag-chain-mount and front-left-leg to newer style mount attachment
    - No longer need to remove 2020 from front front-left-leg if front-drag-chain-mount mounting nuts are forgotten
    - Adds face colors to signify tube routing and improved aesthetics
    [NEMA11-hollow-shaft-stepper.stp, front-drag-chain-mount.FCStd, front-left-leg.FCStd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]
2023-07-29 Replaced solder jumpers with 0ohm
    [limit_switch.kicad_sch, microcontroller.kicad_sch, mobo.kicad_sch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]
2023-07-30 Motor driver new Symbol and fix TVS placement
    [RS485.kicad_sch, aux_header.kicad_sch, aux_headers.kicad_sch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]
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2023-08-01 Updates datum-board-mount for symmetry (DFA Improvement)
    - Adds large chamfers to bottom side to support installation in both +180º/-180º orientation without issue
    [datum-board-mount.FCStd]
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2023-08-14 Initial CAD freeze for v3.1.0 release
    **Extends height of machine by 50mm **
    - This was done to add clearance for tape exiting auto feeders, affects the following parts:
    - `aux-staging-plate-foot`
    - `static camera foot`
    - `front-leg-extension` (new)
    - `back-leg-extension` (new)
    - `front-left-leg` / `front-right-leg`
    - `back-leg`
    **Introduces departures from Stargirl's linear rail mod**
    - Fully removes reference to the `x-gantry-block` design by consolidating features into `x-gantry-back`
    - Updates x-gantry-front to match the M5x40 bolt hole pattern used in `x-gantry-back`
    - Adds better m5-hex-nut insertion clearance to `y-gantry`
    **Improvements to the top-ca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
    [aux-staging-plate-foot.FCStd, back-leg-extension.FCStd, back-leg.FCStd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]
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2023-08-22 Addresses observations from v3.1.0 PVT build
    CAD changes made:
    ⁃ Rounded the ends of the tensioner mounting arms in x-idler-mount to match style of front-####-leg
    ⁃ Added a mid-air hole overhang feature to front-drag-chain-mount’s hex-nut pockets
    ⁃ Tightened the hex-nut pocket on front-left-leg to keep drag-chain mount’s attachment nut in place during transit
    ⁃ Labeled back-leg’s y-stepper wire outlet ports with which side each port is for to help avoid assembly mistakes
    ⁃ Labeled y-gantry-left’s back-leg wire outlet “Y1”
    ⁃ Labeled y-gantry-right’s back-leg wire outlet “Y2”
    ⁃ Added ramped relief cuts on back-leg to divert loose GT2 belt from being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
    [2020-side-printed-pocket-fit-test.FCStd, back-leg-extension.FCStd, back-leg.FCStd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]
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2023-08-29 Fixed parts to address failed Github Action
    [12mm-strip-feeder .FCStd, 12mm-strip-feeder.FCStd, 16mm-strip-feeder .FCStd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]
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2023-08-31 Fine tuning models for printing
    - Adds mid-air hole print optimizations to x-gantry-front
    - Makes it easier insert m3-square-nut into x-gantry-front for top-camera-assembly installation
    - Closes #676
    - Removes chamfer from bottom of top-camera-cover for printability
    - Updates width of nozzle-rack hex-head bolt slots for looser fit
    [top-camera-cover.FCStd]
2023-09-01 Removed alt-view cad assemblies
    removed from repo after no longer needing them during OHAI authoring
    [exploaded-toolhead.FCStd, strip-feeder-mockup-8-12-16-24-32.FCStd, y-gantry-tensioning.FCStd]
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2023-09-06 Reverts strip-feeder designs back to v3.0.5 style
    [12mm-strip-feeder.FCStd, 16mm-strip-feeder.FCStd, 24mm-strip-feeder.FCStd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]
2023-09-06 Adds problematic strip-feeder CAD to branch for cleanup
    [12mm-strip-feeder.FCStd, 16mm-strip-feeder.FCStd, 24mm-strip-feeder.FCStd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]
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2023-09-29 Updates 24mm for hole tolerance and sticker
    [24mm-strip-feeder.FCStd]
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2023-10-02 Fixes adj-strip-feeder for STL export
    Converts the two sides of adj-strip-feeder into a compound shape named "body" so that the BOM utility may render both sides and export an STL comprised of two bodies.
    [x-cable-chain-bracket-alt.FCStd]
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2023-10-02 updates BOM for broken images
    [bom.csv]
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2023-10-13 Adjusts `m5-square-nut` pocket tolerance in `front-left-leg`
    This will prevent the nut used for attaching `front-drag-chain-mount` to `front-left-leg` from free-spinning.
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2023-10-24 Hotfix 8mm-strip-feeder tolerances
    [8mm-strip-feeder.FCStd]
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2023-10-29 Finished reverse polarity and inrush current circuits
    [RS485.kicad_sch, lighting.kicad_sch, microcontroller.kicad_sch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]
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2023-11-01 Reverse polarity placement
    [mobo.kicad_pcb, power.kicad_sch]
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2024-01-11 restores missing N08 nozzle model
    [n08-nozzle.FCStd]
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2024-01-30 Commits work for v3.2.0 release
    - FDM part changes:
    - x-gantry-front
    - switched to using M3x12-self-tapping-screw for installing linear rail and z-limit-switch
    - y-gantry
    - tightened M5 hex nut pocket fit
    - nozzle-rack
    - removed top ribs to improve z-clearance
    - updated mounting bolt channels to reduce likelihood of M3x10-hex-head free-spinning during installation
    - static-camera-foot
    - added bumps mounting socket for tightening fit to bottom-camera-mount
    - mobo-top-cover
    - Added detents to `boot` and `reset` button to improve UX
    - Feeder slot changes:
    - Consolidates the 50x individual feeder slot pieces into 4x subassemblies to reduce assembly time
    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
    [blade-pin-cover.FCStd, blade12-PCB.FCStd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]
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2024-02-06 (Hot fix) better cable fit for `x-cable-chain-bracket-alt`
    [x-cable-chain-bracket-alt.FCStd]
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2024-02-22 FIx STL artifacts zip inside zip
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2024-03-11 begins work on nozzle redesign
    [n045-nozzle.FCStd, n08-nozzle.FCStd, n14-nozzle.FCStd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]
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2024-03-11 Replaces cp40-holder with nozzle-holder
    [2mm-Pin.STEP, 4mmIDx0.6mmCS-o-ring.FCStd, bom.csv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]
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2024-03-21 updates all of the cable harnesses for a rev05 mobo. no lengths are correct yet. many pinouts are still incorrect
    [blade-jumper.bom.tsv, bottom-light.bom.tsv, head.bom.tsv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]
2024-03-21 adds correct lengths to cable harnesses
    [blade-jumper.bom.tsv, y2-motor.yml]
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2024-03-21 adds 3d models with correct relative pathing to local library
    [xy-limit.kicad_pcb, z-limit.kicad_pcb]
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2024-04-16 Fix graphics PCB
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2024-04-17 add missing component which was on the PCB but not on the schematic
    [datum.kicad_pcb, datum.kicad_sch]
2024-04-17 Fix fiducial reference designators
    [datum.kicad_pcb, datum.kicad_sch]
2024-04-17 Fix datum ruler designator
    [datum.kicad_pcb]
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2024-04-17 Fix graphics propoerties
    [datum.kicad_pcb]
2024-04-17 Fix graphics attributes
    [staging-plate.kicad_pcb]
2024-04-17 Fix stagging plate CI
2024-04-17 Fix mounting holes
    [ftp.kicad_pcb, ftp.kicad_sch]
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2024-04-18 Fix part sourcing
    [RS485.kicad_sch, microcontroller.kicad_sch]
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2024-05-17 updates zlimit to rev00b2 with fixed switch pinout
    [z-limit.kicad_pcb, z-limit.kicad_sch]
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2024-05-18 tightens back
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2024-05-22 Tightens the hex nut pockets on y-gantry
    [y-gantry.FCStd]
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2024-07-18 Replaces cp40-nozzle-holder with custom nozzle-holder design
    [2mm-Pin.STEP, 4mmIDx0.6mmCS-o-ring.FCStd, cp40-holder.FCStd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]
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2024-07-18 Updates z-gantry to prevent rubbing on x-idler-pulley bolt
    [z-gantry.FCStd]
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2024-08-09 Corrects name of reducing-union-tea-4-6-4
    [reducing-union-tee-4-6-4.stp]
2024-08-09 Replaces generic camera CAD with specific top/bottom models
    [usb-camera.FCStd]
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2024-08-09 Fixes hole depth for m3-thumb-screw in bottom-camera-mount
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2024-08-12 Attempts to fix diag tree bug in nozzle-camera-mask
    [nozzle-camera-mask.FCStd]
2024-08-12 Cont. attempts to fix diag tree bug in nozzle-camera-mask
    [nozzle-camera-mask.FCStd]
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2024-08-12 fixes BOM broken images
    [bom.csv]
2024-08-12 Attempts to fix broken static-camera-foot image
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2024-09-01 Adjusts tolerances of select FDM parts for easier assembly and less glue
    [nozzle-camera-mask.FCStd, y-gantry-left.FCStd, y-gantry-right.FCStd]
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2024-09-13 reverts ring light to original design with level shifters
    [ringLight.kicad_pcb, ringLight.kicad_sch]
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2025-01-10 fixes x bottom camera offset
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
